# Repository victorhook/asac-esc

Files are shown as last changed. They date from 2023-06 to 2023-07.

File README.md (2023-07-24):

# asac esc

**A** **S**imple **A**nd **C**ool **E**lectronic **S**peed **C**ontroller (asac esc) is an open source ESC, including both hardware and software. The firmware is written in pure C.

## PCB Rev. A

First iteration of PCB is done. All cad files can be found in [kicad/asac-esc-rev-a](kicad/asac-esc-rev-a) and the schematic as PDF can be found there, or in [docs/asac-esc-rev-a.pdf](docs/asac-esc-rev-a.pdf).

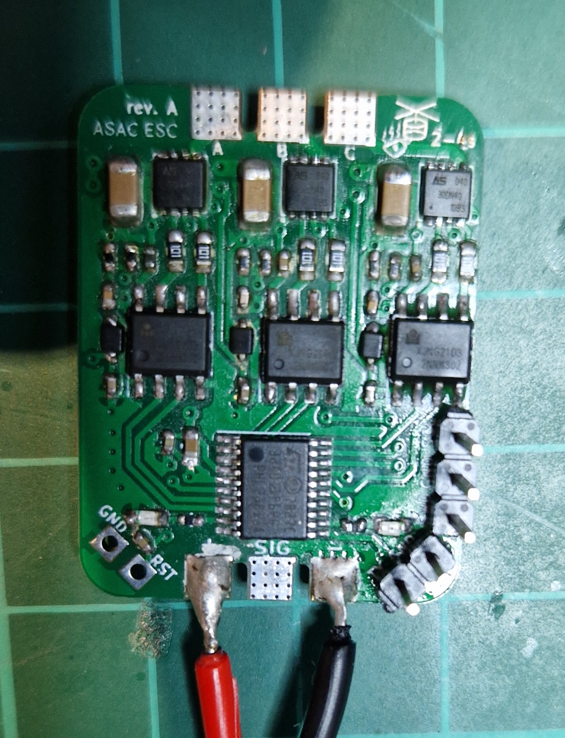
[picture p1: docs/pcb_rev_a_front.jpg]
PCB Rev.A front


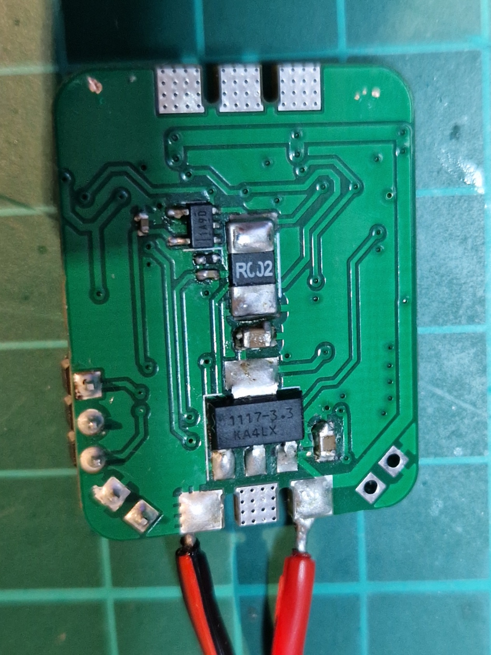
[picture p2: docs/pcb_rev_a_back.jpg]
PCB Rev.A back


## Workings of asac esc

Driving a brushless DC (bldc) motor is done by energizing one of the coils at the time which creates a magnetic field that makes the rotor move due to the magnets on it. Making the rotor move "1 step" is referred to as one *commutation* and making a bldc motor spin is not more complicated than energizing the different coils of the stator repeatedly. How fast a commutation takes will dictate how fast the motor will spin, thus controlling the speed of a bldc motor is done by controlling the speed of the commutations. This is accomplished by driving higher or lower amounts of current through the coils, which creates stronger or weaker magnetic fields, which in turn means that the commutation will be faster or slower.

#### Stator and rotor

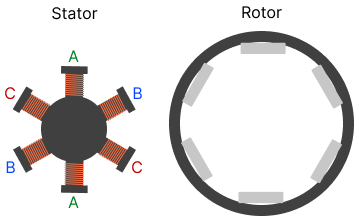
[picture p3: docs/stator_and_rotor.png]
Stator and rotor


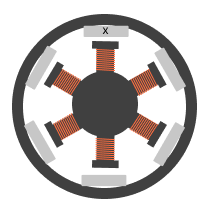
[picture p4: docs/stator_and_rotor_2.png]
Stator and rotor


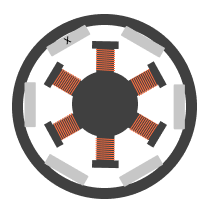
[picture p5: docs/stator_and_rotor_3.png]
Stator and rotor


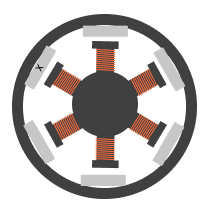
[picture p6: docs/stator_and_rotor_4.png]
Stator and rotor


#### 6-step commutation

Most (perhaps all?) bldc motors has more than 3 coils, but some of the coils are wired together, so that we get only *three* wires out of the motor. We can call each of these wires a *phase*, A, B and C. The commutation sequence consists of 6 unique steps, which then repeats. During each of the 6 steps, one specific phase will get current running into it, and one phase will have current running out of it. Letting current into and out of a phase can be accomplished with the help of mosfets in half-bridge configurations, whereas it's needed with one half-bridge per phase, which means 6 mosfets in total. This way of driving a bldc is motor is referred to as *6-step commutation*.

There are penty of good resources online that describes this process in much detail, such as [here](https://www.digikey.com/en/articles/how-to-power-and-control-brushless-dc-motors).

This image describes the 6 different states. It's slightly simplified, since a "1" doesn't really mean a logic high, nor 1 volt, but simply means that the phase allows current into it, whereas a "0" means that current runs out of the phase. The mosfets are not actually driven by 1s and 0s, but controlled using PWM, which is described in more detail below. The "Z" means that the phase is floating.

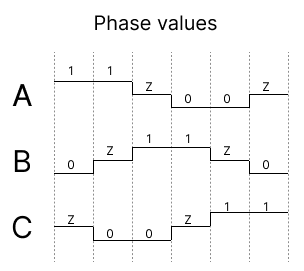
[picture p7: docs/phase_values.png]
Phase values with bemf


Below is an example os the first 2 steps, whereas current runs into phase A and out of phase B, and then out of phase C in step 2.

Commutation state 1 - Current flows into phase **A** and out of **B**.
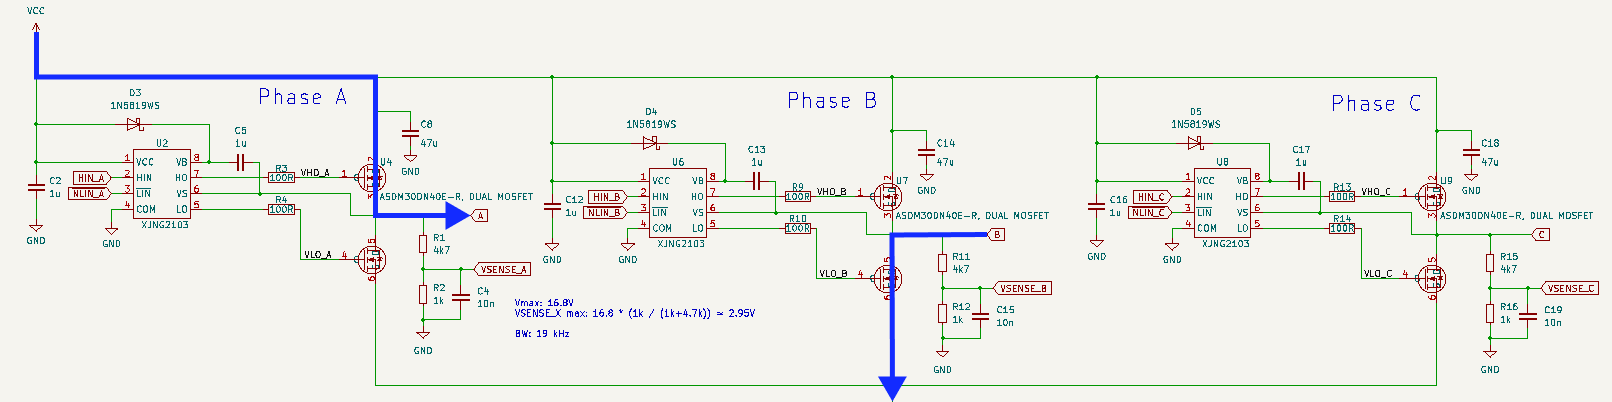
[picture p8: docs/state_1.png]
State 1


Commutation state 2 - Current flows into phase **A** and out of **C**.
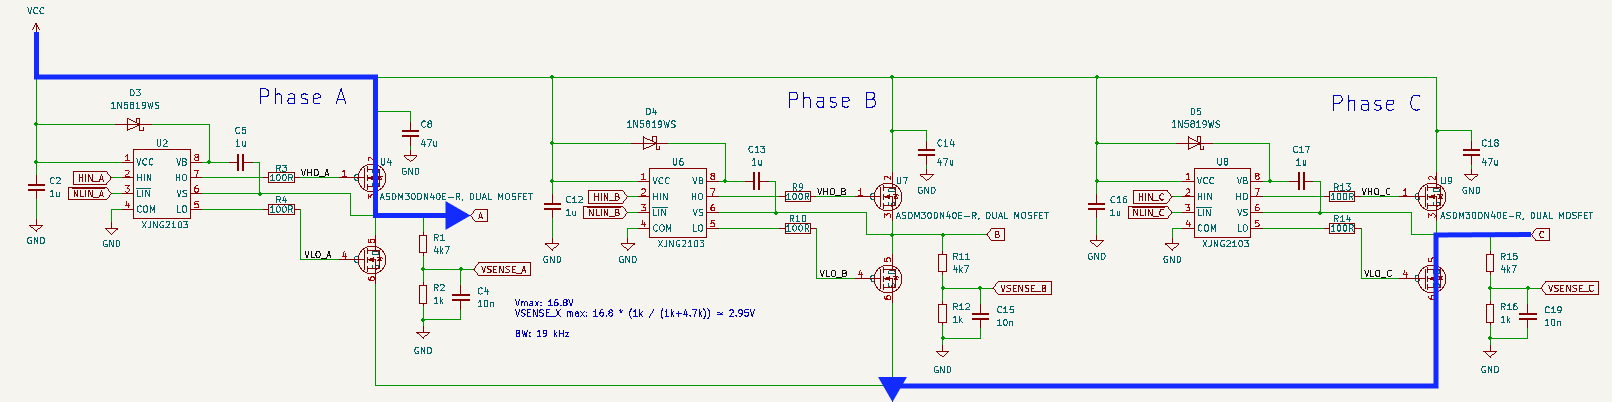
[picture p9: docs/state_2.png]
State 2


And so forth for the steps 4-6...

#### BEMF closed-loop control

While it's possible to run a bldc motor *without* any feedback, it's only going to work at a constrained speed, since we have no indication of where the rotor is. If the position of the rotor is unknown, it's impossible to know exactly *when* to turn on a specific phase, and knowing *when* to do the next commutation can be accomplished by inspecting the back electromotive (bemf) force that is induced in the third ("unused") floating phase. In the schematic above you can see that each phase has a "VSENSE_X" connected to it through a voltage divider. This will be connected to an ADC on the microcontroller.

The bemf will follow (roughly) the pattern as described in the image below:

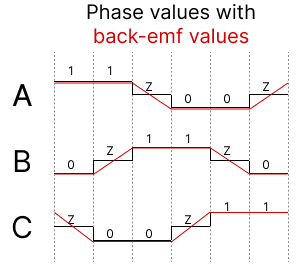
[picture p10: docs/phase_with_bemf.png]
Phase values with bemf


Let's say that we're in step 3, where phase A have just been turned off and left floating. The voltage of the phase is still high, but will after some time go back to zero. The trick here is that we want to detect the middle point of this slope in order to schedule the next commutation. This "middle point" is referred to as *zero cross*. Note that the zero cross is not actually at 0, but the middle point between the highest voltage and zero, thus `zero_cross = vmax / 2`. For this to work we must know which commutation state we're in, since the slope of the bemf-values changes for each state (up/down). The bemf adc value is sampled on each update loop in order to detect when the bemf value crosses the zero cross.

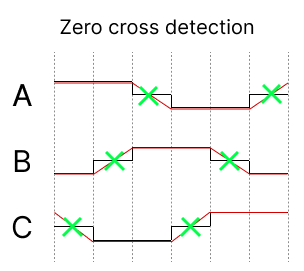
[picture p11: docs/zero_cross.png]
Zero cross


Using bemf as input to know when to switch commutation step is referred to as running in *closed-loop*.

So how do we accomplish this in code? The mosfets that are connected to the high side of the half-bridges are turned on to allow current through, and the mosfets on the low side are driven low to allow current flow through them to ground. Note that the high-side mosfets are driven with a PWM signal which makes it possible to control how much current should flow through the coils. What frequency the PWM signal should have depends on the motor, but asac esc runs PWM on a frequency of 24 kHz (23437.5 Hz) with a duty resolution of 2048. Higher PWM will mean more current -> stronger magnetic field -> faster commutation.

Once a zero cross has been detected, the next commutation is scheduled to be performed in about half a commutation period from the detection. This commutation period time duration is taken from the last commutation period. Note that some delays such as update loop and filtering is subtracted, so in reality the next commutation is scheduled to be something like:
```
if (zero_cross_detected)
{
    next_commutation = now + half_commutation_period - filter_delay - update_delay
}
```

#### Start-up phase
An issue with using back-emf to know when to switch to the next commutation state is that before the motor is spinning we have no knowledge of where the rotor is. A solution to this problem is to start spinning the motor in *open-loop* mode, which means that the commutation states are traversed with a *fixed* period. During this time, the back-emf is still being looked at, to detect when we can switch to closed-loop. This is done if a zero-cross is detected, that seems to come in a "reasonable" time. By "reasonable" time, I mean that its detected roughly in the middle of a commutation period.

#### Input signal
asac esc supports standard input signals such as:
- 50 Hz (1000-2000 us)

These are all in the form of a pulse, whereas the pulse length is directly proportional to the throttle value.

The pulses are detected by an interrupt on the pin.

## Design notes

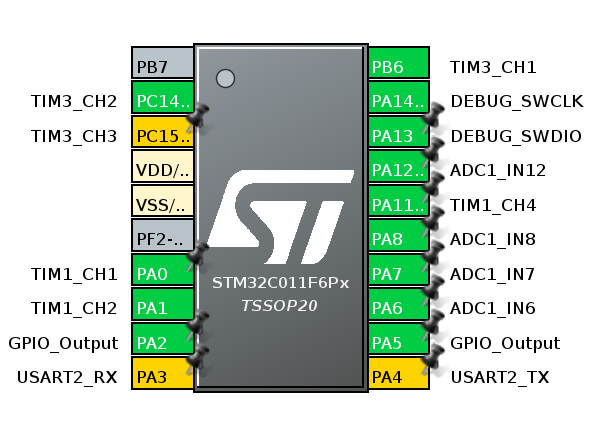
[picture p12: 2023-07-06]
resources/pinout-rev-a.png

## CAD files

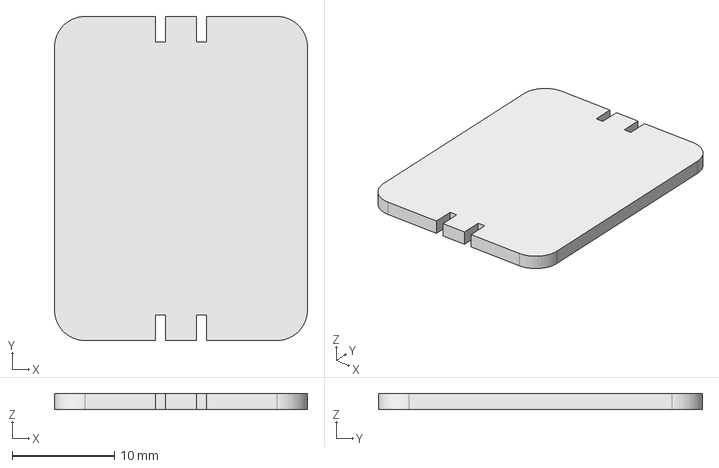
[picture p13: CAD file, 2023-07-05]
cad/pcb.FCStd
24.7 x 31.7 x 1.60 mm

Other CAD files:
cad/pcb-rev-a.stl
cad/pcb-rev-a.dxf

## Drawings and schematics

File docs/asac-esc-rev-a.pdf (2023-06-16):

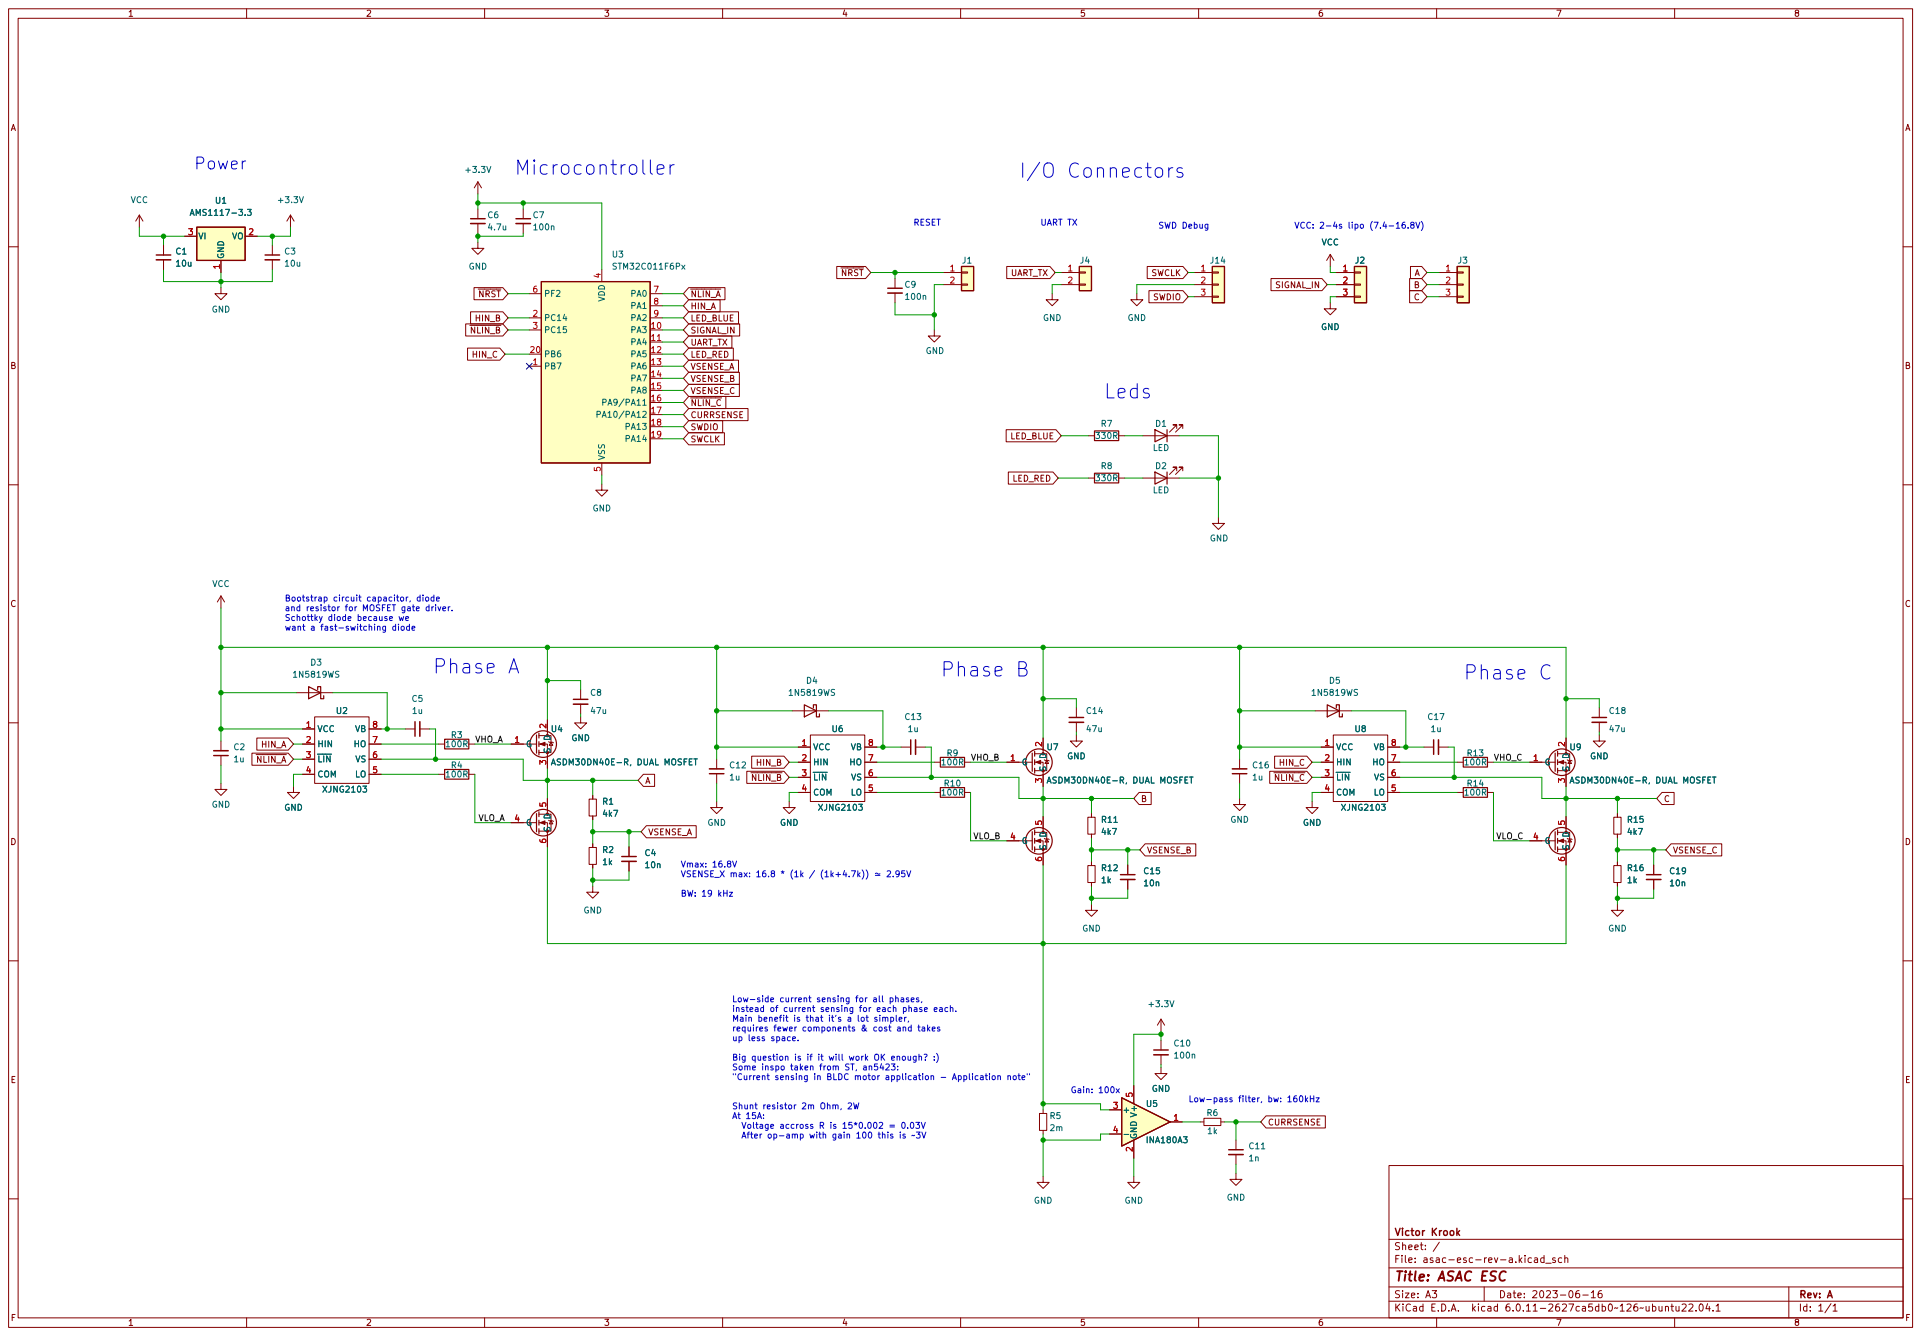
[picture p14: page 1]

instead of current sensing for each phase each. Main benefit is that it's a lot simpler,

Id: 1/1 Title: ASAC ESC

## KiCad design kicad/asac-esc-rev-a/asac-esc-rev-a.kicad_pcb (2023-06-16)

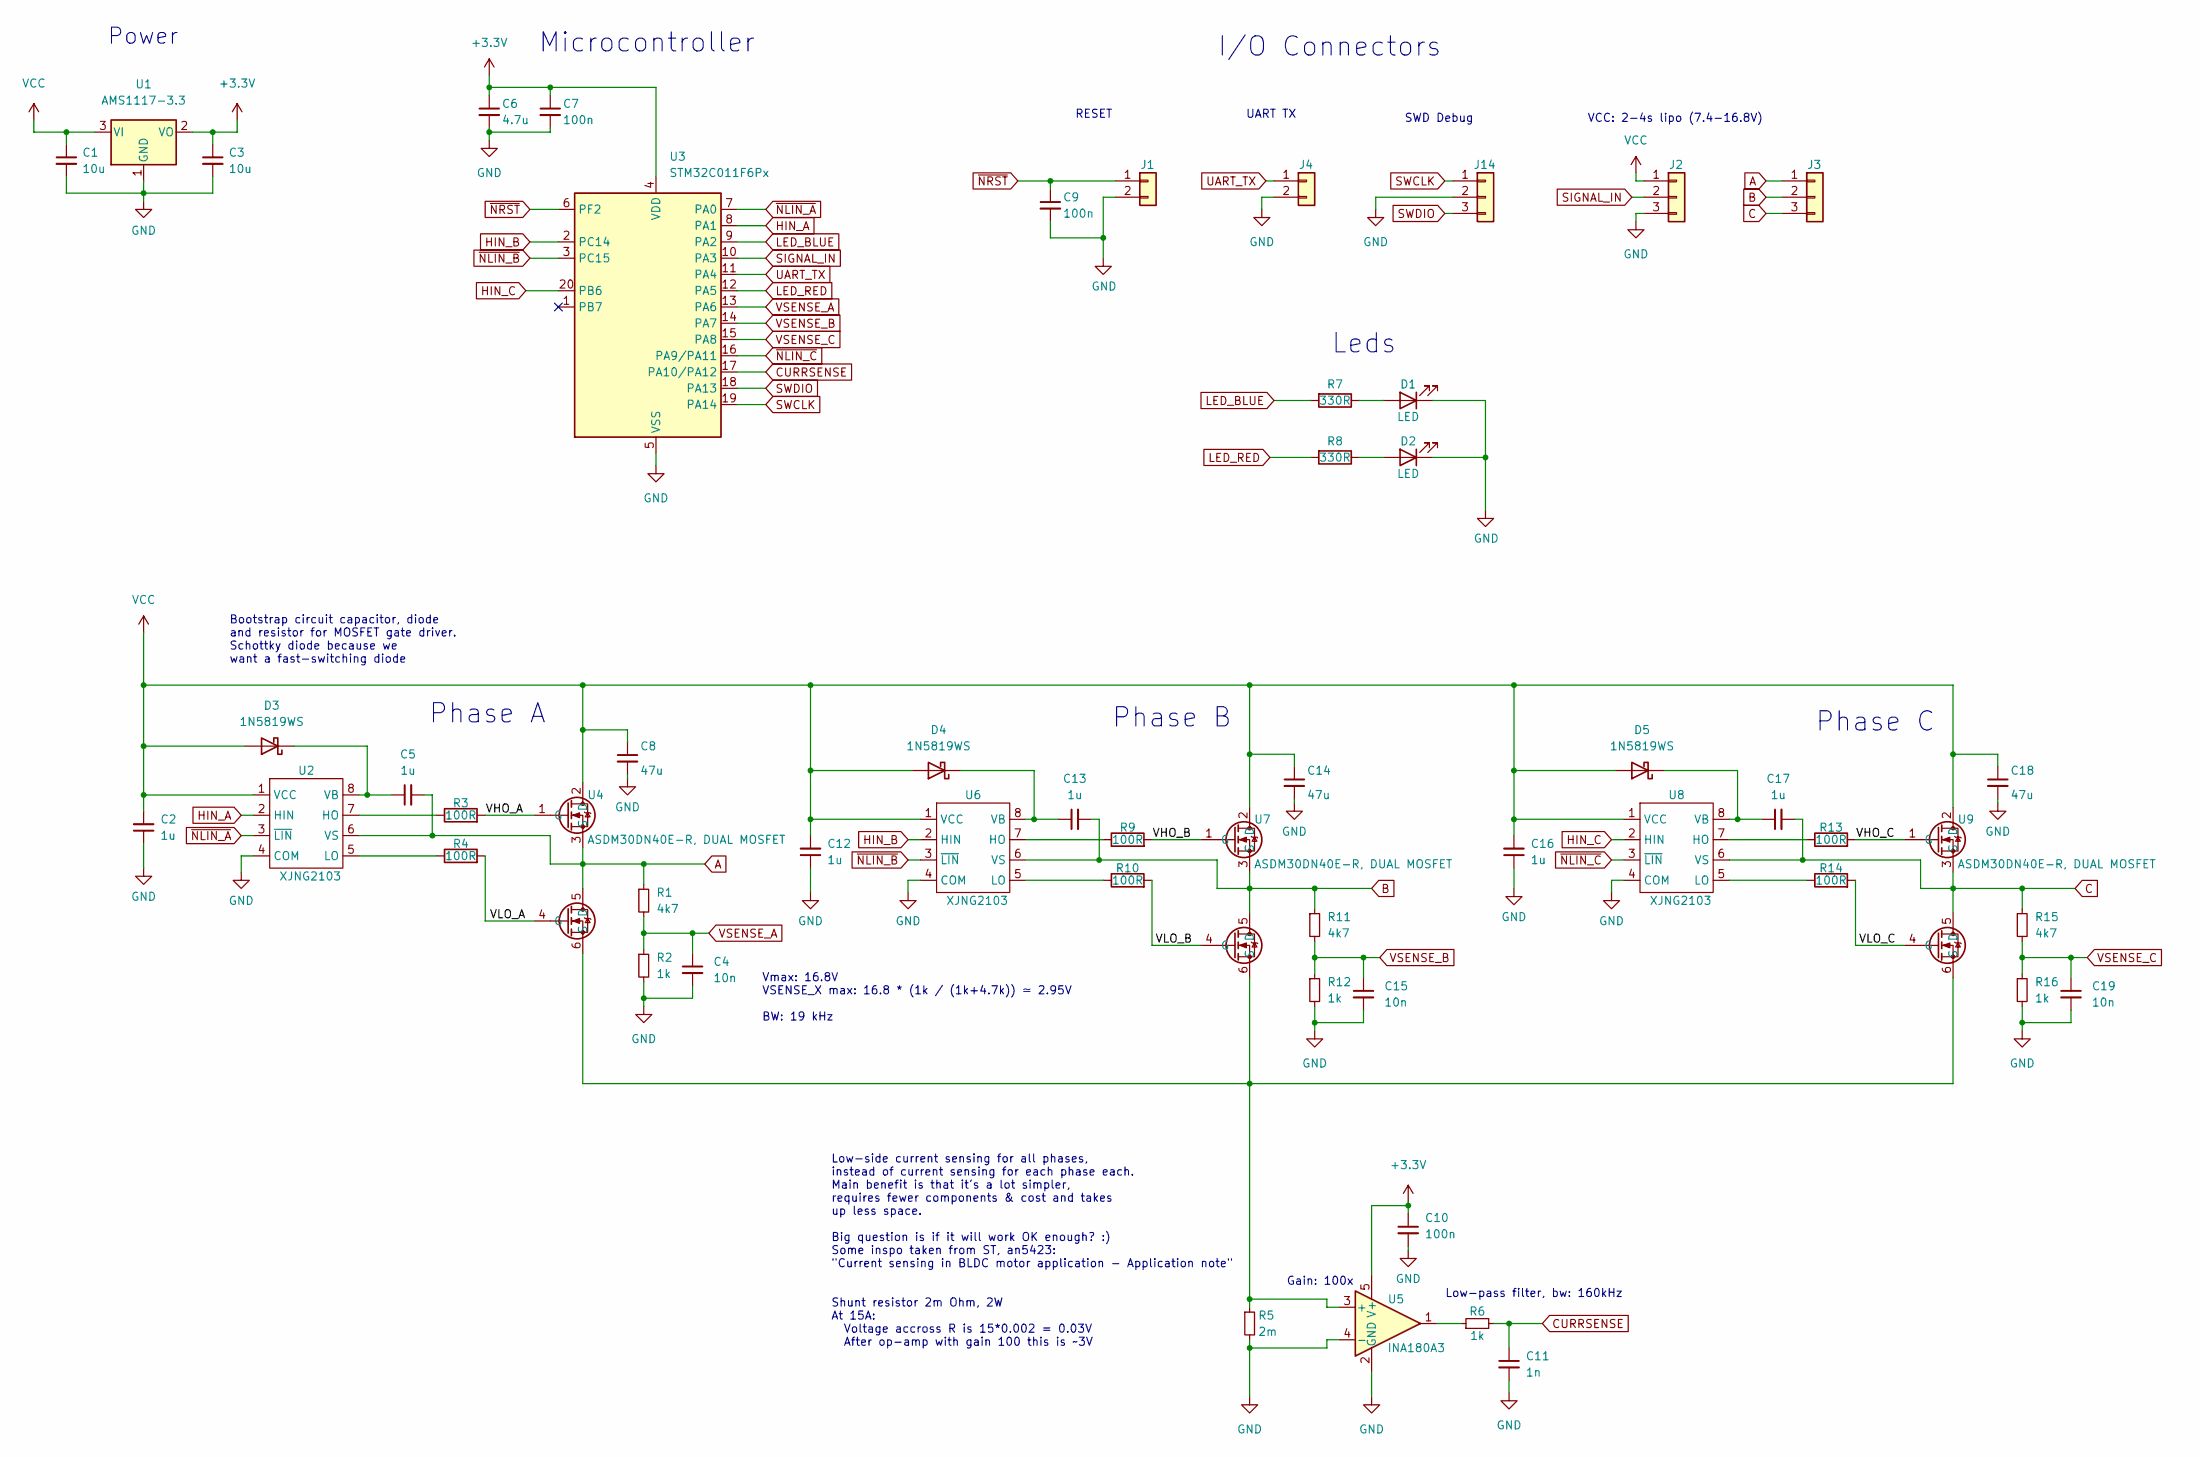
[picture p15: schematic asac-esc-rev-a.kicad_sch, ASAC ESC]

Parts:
C1, C3: 10u; C_0805_2012Metric
C2, C5, C12, C13, C16, C17: 1u; C_0402_1005Metric
C4, C15, C19: 10n; C_0402_1005Metric
C6: 4.7u; C_0603_1608Metric
C7, C9, C10: 100n; C_0402_1005Metric
C8, C14, C18: 47u; C_1206_3216Metric
C11: 1n; C_0402_1005Metric
D1, D2: LED; LED_0603_no_outline
D3, D4, D5: 1N5819WS; D_SOD-323
J1, J4: Conn_01x02_RESET; PinHeader_1x02_P2.54mm_Vertical_No_silk
J2: Conn_01x03; Conn_01x03_BLDC
J3: Motor; Conn_01x03_BLDC
J14: Conn_01x03; PinSocket_1x03_P2.54mm_Vertical_No_silk
R1, R11, R15: 4k7; R_0402_1005Metric
R2, R6, R12, R16: 1k; R_0402_1005Metric
R3, R4, R9, R10, R13, R14: 100R; R_0603_1608Metric
R5: 2m; R_2512_6332Metric
R7, R8: 330R; R_0402_1005Metric
U1: AMS1117-3.3; SOT-223-3_TabPin2
U2, U6, U8: XJNG2103; SOIC-8_3.9x4.9mm_P1.27mm
U3: STM32C011F6Px; TSSOP-20_4.4x6.5mm_P0.65mm
U4, U7, U9: ASDM30DN40E-R, DUAL MOSFET; PDFN3333-8_L3.2-W3.1-P0.65-LS3.4-BL
U5: INA180A3; SOT-23-5

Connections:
+3.3V: C3.1, C6.1, C7.1, C10.1, U1.2 (VO), U3.4 (VDD), U5.5 (V+)
/VHO_A: R3.2, U4.1 (G)
/VHO_B: R9.2, U7.1 (G)
/VHO_C: R13.2, U9.1 (G)
/VLO_A: R4.2, U4.4 (G)
/VLO_B: R10.2, U7.4 (G)
/VLO_C: R14.2, U9.4 (G)
A: C5.2, J3.1, R1.1, U2.6 (VS), U4.3 (S), U4.5 (D)
B: C13.2, J3.2, R11.1, U6.6 (VS), U7.3 (S), U7.5 (D)
C: C17.2, J3.3, R15.1, U8.6 (VS), U9.3 (S), U9.5 (D)
CURRSENSE: C11.1, R6.2, U3.17 (PA10/PA12)
GND: C1.2, C2.1, C3.2, C4.2, C6.2, C7.2, C8.2, C9.2, C10.2, C11.2, C12.1, C14.2, C15.2, C16.1, C18.2, C19.2, D1.1 (K), D2.1 (K), J1.2, J2.3, J4.2, J14.2, R2.2, R5.2, R12.2, R16.2, U1.1 (GND), U2.4 (COM), U3.5 (VSS), U5.2 (GND), U5.4 (-), U6.4 (COM), U8.4 (COM)
HIN_A: U2.2 (HIN), U3.8 (PA1)
HIN_B: U3.2 (PC14), U6.2 (HIN)
HIN_C: U3.20 (PB6), U8.2 (HIN)
LED_BLUE: R7.2, U3.9 (PA2)
LED_RED: R8.2, U3.12 (PA5)
unnamed: C5.1, D3.1 (K), U2.8 (VB)
unnamed: C13.1, D4.1 (K), U6.8 (VB)
unnamed: C17.1, D5.1 (K), U8.8 (VB)
unnamed: D1.2 (A), R7.1
unnamed: D2.2 (A), R8.1
unnamed: R3.1, U2.7 (HO)
unnamed: R4.1, U2.5 (LO)
unnamed: R5.1, U4.6 (S), U5.3 (+), U7.6 (S), U9.6 (S)
unnamed: R6.1, U5.1
unnamed: R9.1, U6.7 (HO)
unnamed: R10.1, U6.5 (LO)
unnamed: R13.1, U8.7 (HO)
unnamed: R14.1, U8.5 (LO)
SIGNAL_IN: J2.2, U3.10 (PA3)
SWCLK: J14.1, U3.19 (PA14)
SWDIO: J14.3, U3.18 (PA13)
UART_TX: J4.1, U3.11 (PA4)
VCC: C1.1, C2.2, C8.1, C12.2, C14.1, C16.2, C18.1, D3.2 (A), D4.2 (A), D5.2 (A), J2.1, U1.3 (VI), U2.1 (VCC), U4.2 (D), U6.1 (VCC), U7.2 (D), U8.1 (VCC), U9.2 (D)
VSENSE_A: C4.1, R1.2, R2.1, U3.13 (PA6)
VSENSE_B: C15.1, R11.2, R12.1, U3.14 (PA7)
VSENSE_C: C19.1, R15.2, R16.1, U3.15 (PA8)
~NLIN_A: U2.3 (~LIN), U3.7 (PA0)
~NLIN_B: U3.3 (PC15), U6.3 (~LIN)
~NLIN_C: U3.16 (PA9/PA11), U8.3 (~LIN)
~NRST: C9.1, J1.1, U3.6 (PF2)

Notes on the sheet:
Phase C
RESET
Leds
Phase B
Gain: 100x
SWD Debug
Low-pass filter, bw: 160kHz
Phase A
I/O Connectors
VCC: 2-4s lipo (7.4-16.8V)
Vmax: 16.8V VSENSE_X max: 16.8 * (1k / (1k+4.7k)) ≃ 2.95V BW: 19 kHz
Power
Bootstrap circuit capacitor, diode and resistor for MOSFET gate driver. Schottky diode because we want a fast-switching diode
UART TX
Low-side current sensing for all phases, instead of current sensing for each phase each. Main benefit is that it's a lot simpler, requires fewer components & cost and takes up less space. Big question is if it will work OK enough? :) Some inspo taken from ST, an5423: "Current sensing in BLDC motor 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
Microcontroller

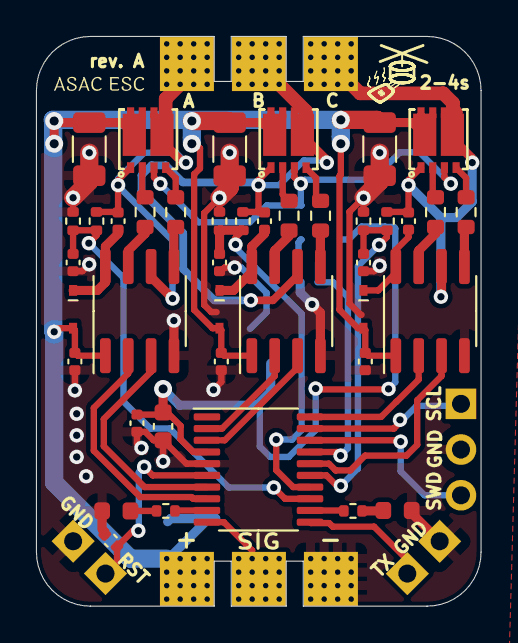
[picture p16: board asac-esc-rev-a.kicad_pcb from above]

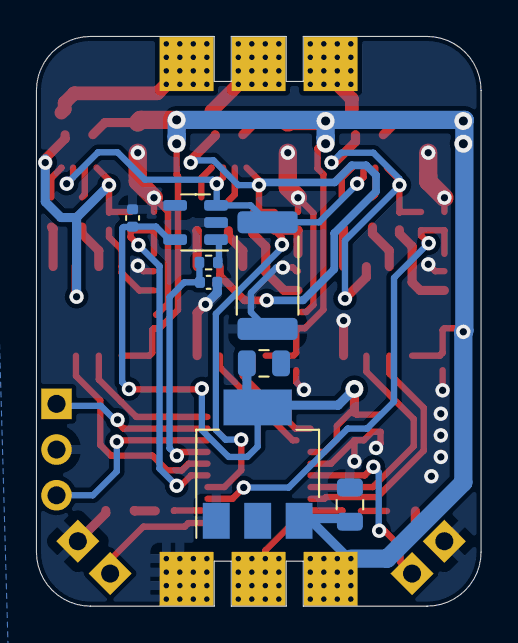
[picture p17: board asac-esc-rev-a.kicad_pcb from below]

Board: 2 copper layers, 24.7 x 31.7 mm, 54 parts (8 on the bottom side), 42 nets.

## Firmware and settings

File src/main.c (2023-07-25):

#include "asac_esc.h"
#include "hal.h"
#include "audio.h"

// Callbacks
void HAL_GPIO_EXTI_Rising_Callback(uint16_t GPIO_Pin);
void HAL_GPIO_EXTI_Falling_Callback(uint16_t GPIO_Pin);

static void blink_boot_up_sequence();
static inline void update_micros_timer();
static inline void switch_to_open_loop();
static inline void update();
static uint32_t read_bemf();
static inline void arm();
static inline void disarm();

/* Returns -1 if the pulse length is invalid */
static inline int16_t pulse_length_to_throttle(const uint32_t time_since_last_pulse);
static void inline set_gpio_mode(GPIO_TypeDef* gpio_port, const uint8_t mode, const uint8_t shift_mask);

static inline void phase_high(__IO uint32_t* pwm_comp_reg, GPIO_TypeDef* nlin_port, uint16_t nlin_pin);
static inline void phase_low(__IO uint32_t* pwm_comp_reg, GPIO_TypeDef* nlin_port, uint16_t nlin_pin);
static inline void phase_input(__IO uint32_t* pwm_comp_reg, GPIO_TypeDef* nlin_port, uint16_t nlin_pin, uint32_t adc_channel);


#define LED_BLUE_HIGH() HAL_GPIO_WritePin(PORT_LED_BLUE, PIN_LED_BLUE, GPIO_PIN_SET)
#define LED_BLUE_LOW() HAL_GPIO_WritePin(PORT_LED_BLUE, PIN_LED_BLUE, GPIO_PIN_RESET)
#define LED_RED_HIGH() HAL_GPIO_WritePin(PORT_LED_RED, PIN_LED_RED, GPIO_PIN_SET)
#define LED_RED_LOW() HAL_GPIO_WritePin(PORT_LED_RED, PIN_LED_RED, GPIO_PIN_RESET)

// Slowest allowed signal is 50 Hz,
#define NO_SIGNAL_RECEIVED_DISARM_TIMEOUT_US (20000 + 10000) // Add some margin

#define MIN_PULSE_LENGTH_US 20
#define MAX_PULSE_LENGTH_US 2500

#define MINIMUM_PULSE_LENGTH_PWM_US        1000
#define MAXIMUM_PULSE_LENGTH_PWM_US        2000
#define MINIMUM_PULSE_LENGTH_ONESHOT125_US 125
#define MAXIMUM_PULSE_LENGTH_ONESHOT125_US 250
#define MINIMUM_PULSE_LENGTH_ONESHOT42_US  42
#define MAXIMUM_PULSE_LENGTH_ONESHOT42_US  84
#define INVALID_PULSE_LENGTH               -1

#define PWM_MIN_DETECTION_LIMIT     750
#define ONESHOT_125_DETECTION_LIMIT 100
#define ONESHOT_4_DETECTION_LIMIT   30

#define MAX_THROTTLE_DUTY_VALUE 2048
#define MIN_THROTTLE_DUTY_VALUE 400

#define PULSE_LENGTH_TO_THROTTLE_FACTOR_PWM        ((1.0 / (float) MINIMUM_PULSE_LENGTH_PWM_US)        * (MAX_THROTTLE_DUTY_VALUE - MIN_THROTTLE_DUTY_VALUE))
#define PULSE_LENGTH_TO_THROTTLE_FACTOR_ONESHOT125 ((1.0 / (float) MINIMUM_PULSE_LENGTH_ONESHOT125_US) * (MAX_THROTTLE_DUTY_VALUE - MIN_THROTTLE_DUTY_VALUE))
#define PULSE_LENGTH_TO_THROTTLE_FACTOR_ONESHOT42  ((1.0 / (float) MINIMUM_PULSE_LENGTH_ONESHOT42_US)  * (MAX_THROTTLE_DUTY_VALUE - MIN_THROTTLE_DUTY_VALUE))

#define phase_a_high()  phase_high( &PWM_REG_HIN_A, PORT_LIN_A, PIN_LIN_A)
#define phase_a_low()   phase_low(  &PWM_REG_HIN_A, PORT_LIN_A, PIN_LIN_A)
#define phase_a_input() phase_input(&PWM_REG_HIN_A, PORT_LIN_A, PIN_LIN_A, ADC_CHANNEL_PHASE_A)
#define phase_b_high()  phase_high( &PWM_REG_HIN_B, PORT_LIN_B, PIN_LIN_B)
#define phase_b_low()   phase_low(  &PWM_REG_HIN_B, PORT_LIN_B, PIN_LIN_B)
#define phase_b_input() phase_input(&PWM_REG_HIN_B, PORT_LIN_B, PIN_LIN_B, ADC_CHANNEL_PHASE_B)
#define phase_c_high()  phase_high( &PWM_REG_HIN_C, PORT_LIN_C, PIN_LIN_C)
#define phase_c_low()   phase_low(  &PWM_REG_HIN_C, PORT_LIN_C, PIN_LIN_C)
#define phase_c_input() phase_input(&PWM_REG_HIN_C, PORT_LIN_C, PIN_LIN_C, ADC_CHANNEL_PHASE_C)


void all_outputs_low()
{
    phase_a_low();
    phase_b_low();
    phase_c_low();
}

// -- Audio -- //

// TODO: Make this a setting?
direction_t direction = DIRECTION_FORWARD;

//#define DO_DEBUG
#define DO_USE_AUDIO


note_t startup_melody[] = {
    {
        .tone            = TONE_B,
        .on_duration_ms  = 100,
        .off_duration_ms = 100
    },
    {
        .tone            = TONE_B,
        .on_duration_ms  = 100,
        .off_duration_ms = 100
    },
    {
        .tone            = TONE_F,
        .on_duration_ms  = 300,
        .off_duration_ms = 0
    }
};

note_t throttle_detected_note = {
    .tone            = TONE_G,
    .on_duration_ms  = 300,
    .off_duration_ms = 300
};

note_t armed_note = {
    .tone            = TONE_B,
    .on_duration_ms  = 300,
    .off_duration_ms = 300
};


int main()
{
    hal_init();
    all_outputs_low();

    blink_boot_up_sequence();
    LED_RED_LOW();
    LED_BLUE_HIGH();

    printf("Starting up...\n");

    #ifdef DO_USE_AUDIO
    play_melody(startup_melody, 3);
    #endif

    while (1)
    {
        update_micros_timer();
        //uint32_t t0 = micros();
        update();
        //uint32_t t1 = micros();
        //uint32_t dt = t1 - t0;
        //printf("%d\n", dt);

        #ifdef DO_DEBUG
        static uint32_t t0 = 0;
        if ((micros() - t0) > 1000000)
        {
            printf("%d, %d\n", state.commutation_mode, state.open_loop_commutations);
            t0 = micros();
        }
        #endif
    }
}

static inline void update()
{
    state_mode_t next_mode;
    uint32_t now = micros();

    long time_since_last_pulse = now - state.signal_last_ok_pulse;

    if ((state.signal_last_ok_pulse > 0) && (time_since_last_pulse < NO_SIGNAL_RECEIVED_DISARM_TIMEOUT_US))
    {
        switch (state.mode)
        {
            case MODE_IDLE:
                // Starting from idle, let's start arming sequence
                next_mode = MODE_ARMING_SEQUENCE_STARTED;
                break;
            case MODE_ARMING_SEQUENCE_STARTED:
                if (state.throttle == 0)
                {
                    next_mode = MODE_ARMED;
                }
                else
                {
                    next_mode = MODE_ARMING_SEQUENCE_STARTED;
                }
                break;
            case MODE_ARMED:
                next_mode = MODE_ARMED;
                break;
            default:
                // Should never reach this
                next_mode = MODE_IDLE;
        }
    }
    else
    {
        next_mode = MODE_IDLE;
    }

    switch (state.mode)
    {
        case MODE_IDLE:
            #ifdef DO_USE_AUDIO
            if (next_mode == MODE_ARMING_SEQUENCE_STARTED)
            {
                play_melody(&throttle_detected_note, 1);
            }
            #endif
            break;
        case MODE_ARMING_SEQUENCE_STARTED:
            if (next_mode == MODE_ARMED)
            {
                arm();
            }
            break;
        case MODE_ARMED:
            if (next_mode == MODE_IDLE)
            {
                disarm();
            }
            else
            {
                if (state.throttle == 0)
                {   // If throttle is zero, we'll switch to open loop control
                    switch_to_open_loop();
                }
                else
                {
                    // Read BEMF ADC value and update highest seen ADC value since last
                    // falling bemf commutation (max 2).
                    uint32_t adc_value = read_bemf();

                    if (adc_value > state.highest_adc_value)
                    {
                        state.highest_adc_value = adc_value;
                    }

                    if (state.commutation_mode == COMMUTATION_OPEN_LOOP)
                    {
                        // -- Open loop commutation -- //

                        bool zero_cross_detected = false;

                        // Check if we've done enough commutations in open-loop
                        // mode and if we've detected a zero cross that seems
                        // to be reasonable.
                        if ((state.open_loop_commutations > state.open_loop_min_commutations) &&
                            (
                                ((state.bemf_rising)  && (adc_value > state.zero_crossing_point)) ||
                                ((!state.bemf_rising) && (adc_value < state.zero_crossing_point))
                            ))
                        {
                            // Zero cross detected. Let's check that the time is reasonable.
                            // We're expecting to detect a zero cross roughly in the middle of
                            // a commutation period.
                            uint32_t expected_zero_cross = state.last_commutation + (state.last_commutation_duration_us / 2);

                            const int offset_limit_plus = 100;
                            const int offset_limit_minus = -100;

                            now = micros();
                            int dt = now - expected_zero_cross;
                            if (dt < 0)
                            {
                                zero_cross_detected = dt > offset_limit_minus;
                            }
                            else
                            {
                                zero_cross_detected = dt < offset_limit_plus;
                            }
                        }

                        if (zero_cross_detected)
                        {   // Detected zero cross in closed-loop!
                            // Let's switch to closed-loop control instead
                            state.commutation_mode = COMMUTATION_CLOSED_LOOP;
                        }
                        else
                        {
                            if (!state.next_commutation_time_set)
                            {
                                state.throttle = state.open_loop_throttle;

                                // Decrease the period a bit to make commutations faster
                                if (state.open_loop_commutation_period_us > 1600)
                                {
                                    state.open_loop_commutation_period_us -= 100;
                                }

                                // We'll set the next commutation to pre-decided time
                                state.next_commutation = now + state.open_loop_commutation_period_us;
                                state.next_commutation_time_set = true;
                                state.open_loop_commutations++;
                            }
                        }
                    }
                    else
                    {   // -- Closed loop commutation -- //

                        // https://dspguru.com/dsp/faqs/fir/properties/
                        // Phase delay of filter: (N – 1) / (2 * Fs) = (5 - 1) / (2 * 60000) ≃ 33us
                        static const uint32_t phase_delay_us = 33;
                        uint16_t loop_delay_us = 12;

                        if ( (!state.next_commutation_time_set) &&
                            (((state.bemf_rising)  && (adc_value > state.zero_crossing_point)) ||
                            ((!state.bemf_rising) &&  (adc_value < state.zero_crossing_point))))
                        {
                            now = micros();
                            state.next_commutation = now + (state.last_commutation_duration_us / 2) - phase_delay_us - loop_delay_us;
                            state.next_commutation_time_set = true;
                        }

                    }

                    if (state.next_commutation_time_set)
                    {
                        now = micros();
                        if (now >= state.next_commutation)
                        {
                            commutate();
                        }
                    }
                }
            }
            break;
    }

    // Transition to next mode
    state.mode = next_mode;
}

void commutate()
{
    /*
        State   A   B   C
          1     1   0   Z
          2     1   Z   0
          3     Z   1   0
          4     0   1   Z
          5     0   Z   1
          6     Z   0   1
    */
    switch (state.bldc_state)
    {
        case BLDC_STATE_1:
            phase_b_low();
            phase_a_high();
            phase_c_input();
            state.bemf_rising = false;
            state.zero_crossing_point = state.highest_adc_value / 2;
            state.highest_adc_value = 0;
            break;
        case BLDC_STATE_2:
            phase_c_low();
            phase_a_high();
            phase_b_input();
            state.bemf_rising = true;
            break;
        case BLDC_STATE_3:
            phase_a_input();
            phase_b_high();
            phase_c_low();
            state.bemf_rising = false;
            state.zero_crossing_point = state.highest_adc_value / 2;
            state.highest_adc_value = 0;
            break;
        case BLDC_STATE_4:
            phase_a_low();
            phase_b_high();
            phase_c_input();
            state.bemf_rising = true;
            break;
        case BLDC_STATE_5:
            phase_a_low();
            phase_b_input();
            phase_c_high();
            state.bemf_rising = false;
            state.zero_crossing_point = state.highest_adc_value / 2;
            state.highest_adc_value = 0;
            break;
        case BLDC_STATE_6:
            phase_a_input();
            phase_b_low();
            phase_c_high();
            state.bemf_rising = true;
            break;
    }

    // Switch to next commutation state
    if (state.direction == DIRECTION_FORWARD)
    {
        state.bldc_state = (state.bldc_state + state.direction) % 6;
    }
    else
    {
        if (state.bldc_state == BLDC_STATE_1)
        {
            state.bldc_state = BLDC_STATE_6;
        }
        else
        {
            state.bldc_state--;
        }
        // In reverse direction, the bemf must also be considered, since the
        // slopes will be reversed.
        state.bemf_rising = !state.bemf_rising;
    }

    // Update time since last transition
    uint32_t now = micros();
    state.last_commutation_duration_us = now - state.last_commutation;
    state.next_commutation_time_set = false;
    state.last_commutation = now;
}

static inline void update_micros_timer()
{
    // If the timer 14 (that handles micro seconds timing) reaches above a
    // certain value, we'll
    const uint32_t UPPER_VALUE = 30000;
    if (TIM14->CNT > UPPER_VALUE)
    {
        state._micros += (TIM14->CNT);
        TIM14->CNT = 0;
    }
}

static inline void switch_to_open_loop()
{
    state.commutation_mode = COMMUTATION_OPEN_LOOP;
    state.open_loop_commutations = 0;
    state.open_loop_commutation_period_us = OPEN_LOOP_START_COMMUTATION_TIME_US;
    state.open_loop_throttle = OPEN_LOOP_THROTTLE;

    reset_commutation_state();
}

void reset_commutation_state()
{
    state.bldc_state = BLDC_STATE_1;
    state.bemf_rising = false;
    all_outputs_low();
}

static uint32_t read_bemf()
{
    while (!(ADC1->ISR & ADC_ISR_EOC));
    uint32_t raw = ADC1->DR;

    // Filter ADC
    for (int i = state.bemf_adc_filter_order-1; i > 0; i--)
    {
        state.bemf_adc_filter[i] = state.bemf_adc_filter[i-1];
    }
    state.bemf_adc_filter[0] = raw;

    uint32_t adc_value = 0;
    for (int i = 0; i < state.bemf_adc_filter_order; i++)
    {
        adc_value += state.bemf_adc_filter[i];
    }

    return adc_value / state.bemf_adc_filter_order;
}

static inline void phase_high(__IO uint32_t* pwm_comp_reg, GPIO_TypeDef* nlin_port, uint16_t nlin_pin)
{
    // Close LIN -> Set NLIN HIGH (Active low)
    nlin_port->BSRR = nlin_pin;
    // Set PWM on HIN to throttle value
    *pwm_comp_reg = state.throttle;
}

static inline void phase_low(__IO uint32_t* pwm_comp_reg, GPIO_TypeDef* nlin_port, uint16_t nlin_pin)
{
    // Open LIN -> Set NLIN LOW (Active low)
    nlin_port->BRR = nlin_pin;
    // Set PWM on HIN to 0
    *pwm_comp_reg = 0;
}

static inline void phase_input(__IO uint32_t* pwm_comp_reg, GPIO_TypeDef* nlin_port, uint16_t nlin_pin, uint32_t adc_channel)
{
    // Close LIN -> Set NLIN LOW (Active low)
    nlin_port->BSRR = nlin_pin;
    // Set PWM on HIN to 0
    *pwm_comp_reg = 0;

    // Stop ADC
    ADC1->CR &= ~ADC_CR_ADSTART;
    // Set channel
    ADC1->CHSELR = adc_channel;
    // Wait for channel selection to be set
    while (!(ADC1->ISR & ADC_ISR_CCRDY));
    // Start ADC again
    ADC1->CR |= ADC_CR_ADSTART;

    state.input_adc_channel = adc_channel;
}

static inline void arm()
{
    #ifdef DO_USE_AUDIO
    play_melody(&armed_note, 1);
    #endif

    state.commutation_mode = COMMUTATION_OPEN_LOOP;
    state.open_loop_commutation_period_us = OPEN_LOOP_START_COMMUTATION_TIME_US;
    LED_RED_HIGH();
    printf("[%lu] ARM\n", millis());
}

static inline void disarm()
{
    state.commutation_mode = COMMUTATION_OPEN_LOOP;
    LED_RED_LOW();
    phase_a_low();
    phase_b_low();
    phase_c_low();
    printf("[%lu] DISARM\n", millis());
}

static inline int16_t pulse_length_to_throttle(const uint32_t pulse_us)
{
    uint32_t pulse;
    uint16_t min;
    float pulse_length_to_throttle_factor;

    /*
        We support the following pulse lengths:
            - 1000-2000 us - Normal 50 Hz PWM
            - 125-250 us - Oneshot 125
            - 42-84 us - Oneshot 42
    */

    if (pulse_us > PWM_MIN_DETECTION_LIMIT)
    {    // PWM
        pulse = constrain(pulse_us, MINIMUM_PULSE_LENGTH_PWM_US, MAXIMUM_PULSE_LENGTH_PWM_US);
        pulse_length_to_throttle_factor = PULSE_LENGTH_TO_THROTTLE_FACTOR_PWM;
        min = MINIMUM_PULSE_LENGTH_PWM_US;
    }
    else if (pulse_us > ONESHOT_125_DETECTION_LIMIT)
    {    // Oneshot 125
        pulse = constrain(pulse_us, MINIMUM_PULSE_LENGTH_ONESHOT125_US, MAXIMUM_PULSE_LENGTH_ONESHOT125_US);
        pulse_length_to_throttle_factor = PULSE_LENGTH_TO_THROTTLE_FACTOR_ONESHOT125;
        min = MINIMUM_PULSE_LENGTH_ONESHOT125_US;
    }
    else if (pulse_us > ONESHOT_4_DETECTION_LIMIT)
    {    // Oneshot 42
        pulse = constrain(pulse_us, MINIMUM_PULSE_LENGTH_ONESHOT42_US, MAXIMUM_PULSE_LENGTH_ONESHOT42_US);
        pulse_length_to_throttle_factor = PULSE_LENGTH_TO_THROTTLE_FACTOR_ONESHOT42;
        min = MINIMUM_PULSE_LENGTH_ONESHOT42_US;
    }
    else
    {    // Unknown??
        return -1;
    }

    // This ensures that as long as there is a desired throttle above 0, it's
    // going to be at least MIN_THROTTLE_DUTY_VALUE. This is because bldc motors
    // are typically very hard to spin at low speeds.
    if (pulse > min)
    {
        return MIN_THROTTLE_DUTY_VALUE + ((uint16_t) ((pulse - min) * pulse_length_to_throttle_factor));
    }
    else
    {
        return 0;
    }
}

static void blink_boot_up_sequence()
{
  for (int i = 0; i < 3; i++)
  {
    LED_RED_HIGH();
    LED_BLUE_LOW();
    HAL_Delay(100);
    LED_RED_LOW();
    LED_BLUE_HIGH();
    HAL_Delay(100);
  }

}

static void inline set_gpio_mode(GPIO_TypeDef* gpio_port, const uint8_t mode, const uint8_t shift_mask)
{
    // To switch between pin mode, eg OUTPUT/INPUT/Alternate function, we
    // set the correct bits in the MODER register:
    // 00: Input
    // 01: Output
    // 10: Alternate function
    // 11: Analog

    // First we'll clear the two bits corresponding to the specific pin
    gpio_port->MODER &= ~(0b11 << shift_mask);
    // Set bits
    gpio_port->MODER |=  (mode << shift_mask);
}


void Error_Handler(void)
{
  LED_BLUE_LOW();
  while (1)
  {
    LED_RED_HIGH();
    HAL_Delay(500);
    LED_RED_LOW();
    HAL_Delay(500);
  }
}

void HAL_GPIO_EXTI_Rising_Callback(uint16_t GPIO_Pin)
{
    disable_interrupts();
    state.signal_last_high_us = micros();
    enable_interrupts();
}

void HAL_GPIO_EXTI_Falling_Callback(uint16_t GPIO_Pin)
{
    disable_interrupts();
    state.signal_last_low_us = micros();

    uint32_t signal_pulse_length_us = state.signal_last_low_us - state.signal_last_high_us;

    if ((signal_pulse_length_us >= MIN_PULSE_LENGTH_US) &&
        (signal_pulse_length_us <= MAX_PULSE_LENGTH_US))
    {
        // Set last signal pulse length to current one
        state.signal_last_pulse_length_us = state.signal_pulse_length_us;

        // Update current pulse length
        state.signal_pulse_length_us = signal_pulse_length_us;

        // Save timestamp of las received OK signal
        state.signal_last_ok_pulse = state.signal_last_low_us;

        // If the newly received signal differs from the previous one, we'll
        // update the throttle value
        if (state.signal_pulse_length_us != state.signal_last_pulse_length_us)
        {   // New pulse received, calculate throttle
            int16_t new_throttle = pulse_length_to_throttle(state.signal_last_pulse_length_us);
            if (new_throttle != INVALID_PULSE_LENGTH)
            {
                // New throttle value set
                state.throttle = new_throttle;
            }
            else
            {
                // Pulse length invalid!
                state.pulse_errors++;
            }
        }
    }
    else
    {
        state.pulse_errors++;
    }
    enable_interrupts();
}

uint32_t micros()
{
  return state._micros + (TIM14->CNT);
}

uint32_t millis()
{
  return micros() / 1000;
}

void sleep_us(const uint32_t delay_us)
{
    uint32_t t0 = micros();
    while ((micros() - t0) < delay_us)
    {
        // Ensure we update microsecond timer while we wait.
        update_micros_timer();
    }
}

void sleep_ms(const uint32_t delay_ms)
{
    sleep_us(delay_ms * 1000);
}

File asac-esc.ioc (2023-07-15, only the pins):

Mcu.UserName=STM32C011F6Px
PA0.Signal=S_TIM1_CH1
PA1.Signal=S_TIM1_CH2
PA13.Signal=DEBUG_SWDIO
PA14-BOOT0.Signal=DEBUG_SWCLK
PA2.Signal=GPIO_Output
PA3.Signal=GPXTI3
PA5.Signal=GPIO_Output
PA6.Signal=ADC1_IN6
PA7.Signal=ADC1_IN7
PA8.Signal=ADC1_IN8
PB6.Signal=S_TIM1_CH3

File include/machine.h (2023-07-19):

#ifndef MACHINE_H
#define MACHINE_H

#define PIN_LED_RED GPIO_PIN_5
#define PORT_LED_RED GPIOA
#define PIN_LED_BLUE GPIO_PIN_2
#define PORT_LED_BLUE GPIOA

// A
#define PIN_HIN_A  GPIO_PIN_1
#define PIN_LIN_A  GPIO_PIN_0
#define PORT_HIN_A GPIOA
#define PORT_LIN_A GPIOA
// B
#define PIN_HIN_B  GPIO_PIN_14
#define PIN_LIN_B  GPIO_PIN_15
#define PORT_HIN_B GPIOC
#define PORT_LIN_B GPIOC
// C
#define PIN_HIN_C  GPIO_PIN_6
#define PIN_LIN_C  GPIO_PIN_11
#define PORT_HIN_C GPIOB
#define PORT_LIN_C GPIOA

#define ADC_CHANNEL_PHASE_A ADC_CHANNEL_6
#define ADC_CHANNEL_PHASE_B ADC_CHANNEL_7
#define ADC_CHANNEL_PHASE_C ADC_CHANNEL_8

//#define ADC_CHANNEL_PHASE_A ADC_CHSELR_CHSEL6
//#define ADC_CHANNEL_PHASE_B ADC_CHSELR_CHSEL7
//#define ADC_CHANNEL_PHASE_C ADC_CHSELR_CHSEL8

#endif /* MACHINE_H */

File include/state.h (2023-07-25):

#ifndef STATE_H
#define STATE_H

#include "stdint.h"
#include "stdbool.h"



#define OPEN_LOOP_START_COMMUTATION_TIME_US 4000
#define OPEN_LOOP_THROTTLE                  500

typedef enum
{
    DIRECTION_FORWARD  = 1,
    DIRECTION_REVERSED = -1
} direction_t;

typedef enum
{
    MODE_IDLE,
    MODE_ARMING_SEQUENCE_STARTED,
    MODE_ARMED,
} state_mode_t;

typedef enum
{
    BLDC_STATE_1 = 0,
    BLDC_STATE_2,
    BLDC_STATE_3,
    BLDC_STATE_4,
    BLDC_STATE_5,
    BLDC_STATE_6,
} bldc_state_t;

typedef enum
{
    COMMUTATION_OPEN_LOOP   = 0,
    COMMUTATION_CLOSED_LOOP = 1
} commutation_mode_t;

typedef struct
{
    // Modes
    state_mode_t       mode;
    commutation_mode_t commutation_mode;

    // Input signal
    uint32_t           signal_last_low_us;
    uint32_t           signal_last_high_us;
    uint32_t           signal_pulse_length_us;
    uint32_t           signal_last_pulse_length_us;
    uint32_t           signal_last_ok_pulse;

    // Commutation
    bldc_state_t       bldc_state;
    bool               bemf_rising;
    uint32_t           last_commutation;
    uint32_t           next_commutation;
    bool               next_commutation_time_set;
    uint32_t           last_commutation_duration_us;
    uint16_t           desired_throttle;
    uint16_t           throttle;
    direction_t        direction;

    // Open loop commutation params
    uint16_t           open_loop_throttle;
    uint16_t           open_loop_delay_us_min;
    uint16_t           open_loop_commutation_period_us;
    uint16_t           open_loop_min_commutations;

    uint16_t           open_loop_commutations;

    // BEMF ADC
    uint32_t           input_adc_channel;
    uint32_t           highest_adc_value;
    uint32_t           zero_crossing_point;
    uint32_t           bemf_adc_filter_order;
    uint32_t           bemf_adc_filter[10];

    // MISC
    uint32_t           pulse_errors;
    uint32_t           _micros;      // Counter for storing microseconds since boot
} state_t;

extern state_t state;


#endif /* STATE_H */

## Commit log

2023-06-11 Created separate sheet for phase A, almost done with it.
    [asac-esc-rev-a.kicad_sch, phase_a.kicad_sch]
2023-06-12 Decided on microcontroller: STM32C011F6P6. The reason for this mcu is that it's quite new, quite cheap, is available on LCSC is developed and maintained by STM. The mcu should have just enough pins f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
    [asac-esc-rev-a.kicad_sch]
2023-06-13 Changed from current sensing each phase to a single current sensing circuit for all MOSFETs. Primary motivation is that it's simpler, let's just hope that it works OK...!
    Pretty much done with schematic now, everything is not
    connected to the MCU yet however, since the layout might
    have an impact on exactly which port should be connected
    where.
    [asac-esc-rev-a.kicad_pcb, asac-esc-rev-a.kicad_sch, phase_a.kicad_sch]
2023-06-16 Did layout and routing of PCB. Rev. A of the PCB is considered done and I have just done the order for PCB and components :)
    [asac-esc-rev-a.kicad_pcb, asac-esc-rev-a.kicad_sch, pcb-rev-a.dxf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]
2023-07-05 Rev. A Done and arrived, time to solder!
    [asac-esc-rev-a-B_Cu.gbr, asac-esc-rev-a-B_Mask.gbr, asac-esc-rev-a-B_Paste.gbr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]
2023-07-06 Firmware project setup
    - Created project in STM32CubeMX
    - Created initial blink sequence in main.c
    - Created json launch file for debugging
    - Added flash-target in makefile to flash
2023-07-15 First test done, managed to spin motor!
    - Moved HAL inits to separate file (hal.c
    for now). Should make a different
    solution for this in the future, but I'd
    like to not follow the CubeMX project
    structure since I don't think it's too
    intuitive.
    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
2023-07-16 Added initial closed-loop control
    - Added ADC handling that reads the
    BEMF from each phase when the
    phase is not active.
    - Made the startup from 0 throttle ->
    to something start with open-loop
    control, whereas it goes over to closed-
    loop control after a while. It's very
    glitchy but works a bit at certain
    throttle levels.
    [machine.h, main.c, state.h]
2023-07-17 Got closed-loop control to work OK, but the logic is somewhat wrong, since the commutation happens at the zero-cross detection, which it should not be. It should happen half a commutation AFTER..?
    [machine.h, main.c, state.h]
2023-07-18 Closed-loop zero detection
    - Added simple check for the zero-cross-detection in closed-loop mode.
    The goal is to have the transition from closed-loop to open-loop smother and
    look for the bemf zero-cross in order to switch mode.
    - Some refactorization, moved most variables to state_t.
2023-07-18 Added images of PCB and updated README
2023-07-19 LED pin bugfix and open-loop improvement
    [machine.h, main.c]
2023-07-22 Refactor and cleanup
    - Put timer 14 (micros()/millis() timer) update logic into a separate
    method, separate from man update function.
    - Made separate method for switching to open loop
    - Some cleanup of variable declarations (eg now, zero_cross_detected)
2023-07-22 Audio support and new mode
    - Added ability to play tones with the motors, as well as melodies.
    - Added new mode (MODE_ARMING_SEQUENCE_STARTED) similar to blheli,
    so so that we require a throttle value of 0 in order to arm.
    - Added support for changing direction to reversed.
    - Added sleep functions, sleep_us and sleep_ms
    [main.c, state.h]
2023-07-24 Added a lot of info and documentation of workings of asac esc
2023-07-25 Refactoring
    - Moved audio methods and definitions to separate module
    - Change audio to consume less power
    - Added oneshot detection, needs to be tested though
    - Turned off/on interrupts on pulse ISR.
    Note sure if this makes any difference..
